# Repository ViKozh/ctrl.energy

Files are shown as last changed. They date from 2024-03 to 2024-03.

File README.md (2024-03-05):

# ctrl.energy
 ESPHome-based node for energy monitoring with additional functionality

## Brief Description
 This module made for my own house as main power meter sensor and gate / outdoor lights control. There're two ESP32 nodes on PCB. One of them performs energy meter monitoring via RS-485 / MODBUS interface. Another one is used to control sliding gates control with Wiegand-based keys and outdoor lights. Also it monitors gate state.

## Hardware
 IMPORTANT!!! Working with HOT LINE AC is dangerous and could harm or even kill! Don't do anything if you don't know how it could behave.
 IMPORTANT 2!!! This hardware works from DC12 power source (J2). It can commutate 5 channels of 16A 230AC via K2-K5 relays.

 You can view PCB and schematic in the _/hardware_ folder in this repository. It was made in KiCAD, so you don't need to buy expensive PCB toolkit to modify or view it. Just keep in mind following mistakes (not the only these, I suppose):
  - Incorrect placements for reed switch based relays (K7 and K8). I've found this error only when recieved produced PCBs - so I decided not to fix it.
  - You'll need better heatsink. LM1084-3.3 could be very hot when powered by 12V. So you should use good thermal interface for it.

 *Note*: PCB successfully soldered and working well (it works almost two weeks.)

## Capabilities

### Energy control node:
  - Temperature monitoring in House Energy Box via D18B20 sensor (J1).
  - Monitor UPS state: battery health (binary sensor) and main power source state (binary sensor) (J3).
  - Monitor state of main power circuit breaker (J4) with auxilary contact like [this](https://automationforum.co/what-is-auxiliary-contact-and-how-it-works-with-mcb/).
  - Monitor case intrusion to House Energy Box via switch connected to J6.
  - Writing logs and settings to microSD card module (J18).
  - Integrated ds3232 RTC clock (EEPROM and alarms functionality is currently not supported by ESPHome) + cr2032 lithium battery.
  - Modbus / RS485 interface via RS485 to UART converter (J12).
  - UART logs from ESP32 (J9).
  - Power Control for Gate control node to reduce power consumption when Main Power source is off the grid.
  - Send messages of problems, daily and monthly report via Telegram Bot (you should create it, see Telegram bot reference to know how to create own telegram bot).

### Gate control node:
  - Control sliding gates in two modes (i.e. full open mode and pedestrian mode) (J16).
  - Sense gate state (opened or closed) with any switch or button (J17).
  - Stores up to 8 Wiegand-26 keys to open gate - use *+ KEY* (SW3) to add a new key, short press *- KEY* (SW4) to remove one key, long press *- KEY* to remove all keys from memory of ESP32.
  - RFID (Wiegand-26 protocol) with J15 pins 5-8.
  - Indicates success or failure with red/green LEDs (J15, pins 2 and 3 as control _ground pins_, pin 1 as +12V power pin for LEDs)
  - Controls up to 5 lamps/zones (*HOT ZONE!!! Up to AC 230v*) - connect AC power source to J5, connect lamps to J7, J8, J10, J11 and J13.

## Configuration

### Energy control node:

  You should configure _secrets.yaml_ to use telegram bot. Both *tg_token_id* and *tg_chat_id* are required for messaging. 

  Set *pincode* to define code to arm/disarm case intrusion protection.

  Set *energy_provider_name* to you Energy Company name or anything else.

  Set *ha_url* to your Home Assistant instance URL and *grafana_url* to Grafana Dashboard. This links will be available in telegram messages.

  Another options are pretty common for ESPHome configs. See _config.yaml_ for all required variables.

### Gate control node:

  This node configuration is also contains common for ESPHome secret variables.

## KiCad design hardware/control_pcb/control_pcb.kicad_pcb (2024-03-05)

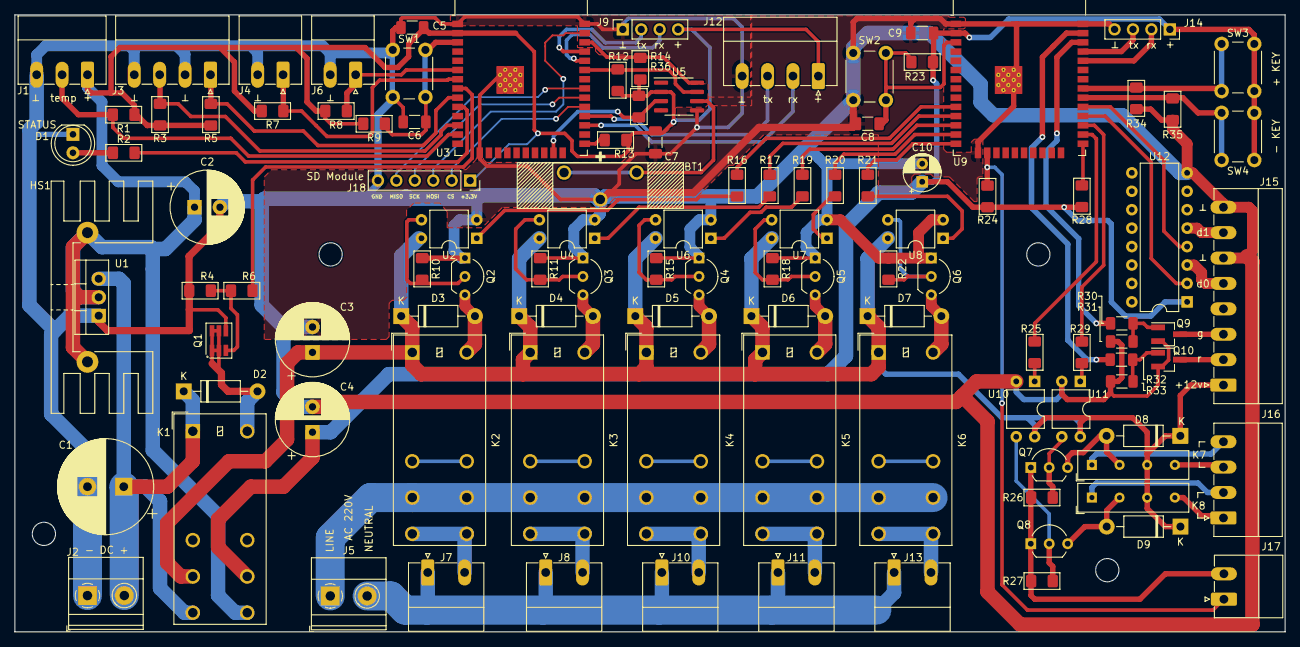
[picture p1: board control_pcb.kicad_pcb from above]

Board: 2 copper layers, 175.0 x 85.0 mm, 109 parts (0 on the bottom side), 85 nets.

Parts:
BT1: CR2032; Battery_Holder_CR2032_Vertical
C1: 1000uF / 50v; CP_Radial_D13.0mm_P5.00mm
C2, C4: 100uF / 16v; CP_Radial_D10.0mm_P3.50mm
C3: 100uF / 50v; CP_Radial_D10.0mm_P3.50mm
C5, C7, C9: 100nF; C_1206_3216Metric_Pad1.33x1.80mm_HandSolder
C6, C8: 1uF; C_1206_3216Metric_Pad1.33x1.80mm_HandSolder
C10: 10uF / 16v; CP_Radial_D5.0mm_P2.50mm
D1: STATUS; LED_D5.0mm_Clear
D2: 1N4002; D_DO-41_SOD81_P10.16mm_Horizontal
D3, D4, D5, D6, D7, D8, D9: 1N4007; D_DO-41_SOD81_P10.16mm_Horizontal
HS1: Heatsink_Pad; Heatsink_Stonecold_HS-132_32x14mm_2xFixation1.5mm
J1: DS18B20 TEMP; PhoenixContact_MC_1,5_3-G-3.5_1x03_P3.50mm_Horizontal
J2: DC12v; TerminalBlock_Phoenix_MKDS-1,5-2-5.08_1x02_P5.08mm_Horizont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
J3: UPS_DETECTION; PhoenixContact_MC_1,5_4-G-3.5_1x04_P3.50mm_Horizontal
J4: INPUT_FUSE_SENSE; PhoenixContact_MC_1,5_2-G-3.5_1x02_P3.50mm_Horizontal
J5: AC IN; TerminalBlock_Phoenix_MKDS-1,5-2-5.08_1x02_P5.08mm_Horizont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
J6: CASE_SENSOR; PhoenixContact_MC_1,5_2-G-3.5_1x02_P3.50mm_Horizontal
J7: Parking; PhoenixContact_MC_1,5_2-G-5.08_1x02_P5.08mm_Horizontal
J8: Front Yard; PhoenixContact_MC_1,5_2-G-5.08_1x02_P5.08mm_Horizontal
J9: EC_RS232; PinSocket_1x04_P2.54mm_Vertical
J10: Bollards; PhoenixContact_MC_1,5_2-G-5.08_1x02_P5.08mm_Horizontal
J11: Address; PhoenixContact_MC_1,5_2-G-5.08_1x02_P5.08mm_Horizontal
J12: MODBUS_UART; PhoenixContact_MC_1,5_4-G-3.5_1x04_P3.50mm_Horizontal
J13: Fence Lights; PhoenixContact_MC_1,5_2-G-5.08_1x02_P5.08mm_Horizontal
J14: LC_RS232; PinSocket_1x04_P2.54mm_Vertical
J15: RFID_READER; PhoenixContact_MC_1,5_8-G-3.5_1x08_P3.50mm_Horizontal
J16: GATES_CONTROL; PhoenixContact_MC_1,5_4-G-3.5_1x04_P3.50mm_Horizontal
J17: GATES_STATE_SWITCH; PhoenixContact_MC_1,5_2-G-3.5_1x02_P3.50mm_Horizontal
J18: SD Module; PinSocket_1x06_P2.54mm_Vertical
K1: G2RL-2; Relay_DPDT_Omron_G2RL-2
K2, K3, K4, K5, K6: G2RL-1-E; Relay_SPDT_Omron_G2RL-1-E
K7, K8: EDR101A1200; Relay_SPST_StandexMeder_MS_Form1AB
Q1: AO6400; SOT-23-6_Handsoldering
Q2, Q3, Q4, Q5, Q6, Q7, Q8: 2N2222; TO-92_Inline_Wide
Q9, Q10: IRLML2402; SOT-23_Handsoldering
R1: 4k7; R_1206_3216Metric_Pad1.42x1.75mm_HandSolder
R2: 68; R_1206_3216Metric_Pad1.42x1.75mm_HandSolder
R3, R4, R5, R7, R8, R9, R10, R11, R12, R13, R14, R15, R18, R22, R23, R24, R26, R27, R28, R34, R35, R36: 10k; R_1206_3216Metric_Pad1.42x1.75mm_HandSolder
R6: 150; R_1206_3216Metric_Pad1.42x1.75mm_HandSolder
R16, R17, R19, R20, R21, R25, R29: 120; R_1206_3216Metric_Pad1.42x1.75mm_HandSolder
R30, R32: 1k; R_1206_3216Metric_Pad1.30x1.75mm_HandSolder
R31, R33: 100k; R_1206_3216Metric_Pad1.30x1.75mm_HandSolder
SW1: EC_RESET; SW_PUSH_6mm
SW2: GLC_RESET; SW_PUSH_6mm
SW3: Write Token; SW_PUSH_6mm
SW4: Delete Token; SW_PUSH_6mm
U1: LM1084-3.3; TO-220-3_Vertical
U2, U4, U6, U7, U8, U10, U11: PC817; DIP-4_W7.62mm
U3, U9: ESP32-WROOM-32; ESP32-WROOM-32D
U5: DS3232M; SOIC-8_3.9x4.9mm_P1.27mm
U12: DIP-16_W7.62mm

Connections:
/+3.3V: C4.1, C9.2, C10.1, J14.1, K1.21, R23.2, R24.1, R28.1, SW3.2, SW4.2, U9.2 (VDD), U12.1 (Vdd)
/+3.3V_PROTECTED: C2.1, C5.2, C7.2, HS1.1, J1.1, J9.4, J12.1, J18.1, K1.24, R1.1, R3.2, R5.2, R7.2, R8.2, R9.2, R12.2, R13.1, R14.2, R36.1, U1.2 (VO), U3.2 (VDD), U5.2 (VCC)
/+12V: C3.1, D3.1 (K), D4.1 (K), D5.1 (K), D6.1 (K), D7.1 (K), D8.1 (K), D9.1 (K), J15.1, K1.11, K2.A1, K3.A1, K4.A1, K5.A1, K6.A1, K7.5, K8.5, U2.4, U4.4, U6.4, U7.4, U8.4, U10.4, U11.4
/Energy Control/AC_LOW: J3.3, R3.1, U3.12 (IO27)
/Energy Control/BAT_LOW: J3.1, R5.1, U3.9 (IO33)
/Energy Control/CASE_OPEN: J6.1, R8.1, U3.6 (IO34)
/Energy Control/EC_M_RX: J12.2, U3.27 (IO16)
/Energy Control/EC_M_TX: J12.3, U3.28 (IO17)
/Energy Control/EC_RX: J9.3, U3.34 (RXD0/IO3)
/Energy Control/EC_TX: J9.2, U3.35 (TXD0/IO1)
/Energy Control/INPUT_FUSE: J4.1, R7.1, U3.7 (IO35)
/Energy Control/INT_TEMP: J1.2, R1.2, U3.13 (IO14)
/Energy Control/SCL: R14.1, U3.36 (IO22), U5.8 (SCL)
/Energy Control/SDA: R12.1, U3.33 (IO21), U5.7 (SDA)
/Energy Control/SD_CS: J18.2, U3.29 (IO5)
/Energy Control/SD_MISO: J18.5, U3.31 (IO19)
/Energy Control/SD_MOSI: J18.3, U3.37 (IO23)
/Energy Control/SD_SCK: J18.4, U3.30 (IO18)
/Energy Control/TACT_FREQ: R36.2, U3.23 (IO15), U5.3 (~INT/SQW)
/LIGHT_00: R16.1, U9.10 (IO25)
/LIGHT_01: R17.1, U9.11 (IO26)
/LIGHT_02: R19.1, U9.12 (IO27)
/LIGHT_03: R20.1, U9.13 (IO14)
/LIGHT_04: R21.1, U9.14 (IO12)
/Lights Relays/LINE: J5.1, K2.11, K3.11, K4.11, K5.11, K6.11
/Lights Relays/NEUTRAL: J5.2, J7.1, J8.1, J10.1, J11.1, J13.1
/OPEN_GATE: R25.2, U9.26 (IO4)
/OPEN_PEDS: R29.2, U9.27 (IO16)
/POW_CTRL: R6.1, U3.8 (IO32)
/SENS_GATE: J17.1, R24.2, U9.16 (IO13)
/WD_0: U9.28 (IO17), U12.2 (Out_A)
/WD_1: U9.29 (IO5), U12.4 (Out_B)
/WLED_GREEN: R30.1, U9.36 (IO22)
/WLED_RED: R32.1, U9.37 (IO23)
/Wiegand Converter/LED_CTRL_GREEN: J15.3, Q9.3 (D)
/Wiegand Converter/LED_CTRL_RED: J15.2, Q10.3 (D)
/Wiegand Converter/WIEGAND_D0: J15.5, U12.3 (In_A)
/Wiegand Converter/WIEGAND_D1: J15.7, U12.5 (In_B)
GND: BT1.2 (-), C1.2, C2.2, C3.2, C4.2, C5.1, C6.2, C7.1, C8.2, C9.1, C10.2, D1.1 (K), J1.3, J2.1, J3.2, J3.4, J4.2, J6.2, J9.1, J12.4, J14.4, J15.6, J15.8, J17.2, J18.6, Q1.4 (S), Q2.1 (E), Q3.1 (E), Q4.1 (E), Q5.1 (E), Q6.1 (E), Q7.1 (E), Q8.1 (E), Q9.2 (S), Q10.2 (S), R4.2, R10.1, R11.1, R15.1, R18.1, R22.1, R26.2, R27.2, R31.1, R33.1, R34.1, R35.1, SW1.1, SW2.1, U1.1 (GND), U2.2, U3.1 (GND), U3.15 (GND), U3.38 (GND), U3.39 (GND), U4.2, U5.5 (GND), U6.2, U7.2, U8.2, U9.1 (GND), U9.15 (GND), U9.38 (GND), U9.39 (GND), U10.2, U11.2, U12.8 (Vss)
unnamed: BT1.1 (+), U5.6 (VBAT)
unnamed: D1.2 (A), R2.1
unnamed: D2.2 (A), K1.A2, Q1.1 (D), Q1.2 (D), Q1.5 (D), Q1.6 (D)
unnamed: C1.1, D2.1 (K), J2.2, K1.14, K1.A1, U1.3 (VI)
unnamed: D3.2 (A), K2.A2, Q2.3 (C)
unnamed: D4.2 (A), K3.A2, Q3.3 (C)
unnamed: D5.2 (A), K4.A2, Q4.3 (C)
unnamed: D6.2 (A), K5.A2, Q5.3 (C)
unnamed: D7.2 (A), K6.A2, Q6.3 (C)
unnamed: D8.2 (A), K7.3, Q7.3 (C)
unnamed: D9.2 (A), K8.3, Q8.3 (C)
unnamed: J7.2, K2.14
unnamed: J8.2, K3.14
unnamed: J10.2, K4.14
unnamed: J11.2, K5.14
unnamed: J13.2, K6.14
unnamed: J14.2, U9.34 (RXD0/IO3)
unnamed: J14.3, U9.35 (TXD0/IO1)
unnamed: J16.1, K8.7
unnamed: J16.2, K8.1
unnamed: J16.3, K7.7
unnamed: J16.4, K7.1
unnamed: Q1.3 (G), R4.1, R6.2
unnamed: Q2.2 (B), R10.2, U2.3
unnamed: Q3.2 (B), R11.2, U4.3
unnamed: Q4.2 (B), R15.2, U6.3
unnamed: Q5.2 (B), R18.2, U7.3
unnamed: Q6.2 (B), R22.2, U8.3
unnamed: Q7.2 (B), R26.1, U11.3
unnamed: Q8.2 (B), R27.1, U10.3
unnamed: Q9.1 (G), R30.2, R31.2
unnamed: Q10.1 (G), R32.2, R33.2
unnamed: R16.2, U2.1
unnamed: R17.2, U4.1
unnamed: R19.2, U6.1
unnamed: R20.2, U7.1
unnamed: R21.2, U8.1
unnamed: R25.1, U10.1
unnamed: R29.1, U11.1
unnamed: C6.1, R9.1, SW1.2, U3.3 (EN)
unnamed: R13.2, U3.25 (IO0)
unnamed: R2.2, U3.10 (IO25)
unnamed: C8.1, R23.1, SW2.2, U9.3 (EN)
unnamed: R28.2, U9.25 (IO0)
unnamed: R35.2, SW4.1, U9.30 (IO18)
unnamed: R34.2, SW3.1, U9.31 (IO19)

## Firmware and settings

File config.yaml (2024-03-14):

substitutions:
  voltage_normal: '230'
  supported_load_level: '32'
  voltage_min_bound: '120'
  voltage_max_bound: '280'
  voltage_warning_lower_level: '170'
  voltage_warning_upper_level: '240'
  voltage_failure_lower_level: '150'
  voltage_failure_upper_level: '270'
  phase_shift_warning_level: '5.0'
  phase_shift_failure_level: '20.0'
  overload_warning_level: '5.0'
  overload_failure_level: '20.0'
  energy_source_name: !secret energy_provider
  tg_bot_token: !secret tg_token_id
  tg_chat_id: !secret tg_chat_id
  grafana_url: !secret grafana_url
  ha_url: !secret ha_url
  case_pincode: !secret pincode

esphome:
  name: energy-control
  comment: Energy Control
  project:
    name: "vks.control_energy"
    version: "1.1"
  libraries:
    - SPI
    - FS
    - SD
    - FFat
    - ArduinoJson
  includes:
    - csv_strings.h
    - tg_bot_strings.h
    - log_strings.h
    - sdcard.h
    - settings.h
    - problems.h
    - snapshot.h
  platformio_options:
    build_flags: -DFS_NO_GLOBALS
    lib_ldf_mode: deep+    
  on_boot:
    priority: 600
    then:
      - ds1307.read_time: rtc_clock
      - if:
          condition:
            - lambda: return id(disable_deep_sleep);
          then:
            - deep_sleep.prevent: dsleep
      - lambda: |-
          setupProblems();

          //Set Generic Power Failure to warning (undefined state) until connection to MODBUS sensor is stabilized or failed.
          setProblem(Problems::GENERIC_POWER_FAILURE, ProblemState::WARNING);
          ESP_LOGI("Energy Meter", "Is module offline? %s", YESNO(id(main_energy_meter).get_module_offline()));

          id(card_available) = SD.begin(5);

          if(!id(card_available)) {
            ESP_LOGW("SD", "Unable to mount SD card.");
          } else {
            sdcard::writeLogfile(id(rtc_clock).utcnow(), LOG_EVENT_TYPE_INFO, LOG_CATEGORY_NODE, "Node is starting...");
          }

          settings::storage = &id(system_settings)[0];
          ESP_LOGD("Settings", "Loading settings...");
          if(!settings::readSettings()) {
            ESP_LOGE("Settings", "Unable to initialize settings data.");
          }
          

          auto counter = id(em_x_total_counter).state;
          for(int i = 0; i < sizeof(snapData.data); i++) {
            snapData.data[i] = id(snapshot_data)[i];
          };
          if(!isfinite(counter)) {
            ESP_LOGW("Counter", "Power meter consumption counter data is unavailable. Maybe counter is offline?");
          }
          loadFromSnapshot(counter);

          
          add_on_failure_callback([](Problems problem) { 
            id(process_problem).execute(
              static_cast<int>(problem),
              static_cast<int>(ProblemState::FAILURE)
              ); });
          add_on_warning_callback([](Problems problem) { 
            id(process_problem).execute(
              static_cast<int>(problem), 
              static_cast<int>(ProblemState::WARNING)
              ); });
          add_on_restore_callback([](Problems problem) { 
            id(process_problem).execute(
              static_cast<int>(problem),
              static_cast<int>(ProblemState::NONE)
              ); });

          if(!id(card_available)) {
            ESP_LOGW("SD", "Unable to mount SD card.");
          } else {
            sdcard::writeLogfile(id(rtc_clock).utcnow(), LOG_EVENT_TYPE_INFO, LOG_CATEGORY_NODE, "Node has been started.");
          }
      - delay: 2s
      - wait_until:
          condition:
            lambda: return id(rtc_clock).now().is_valid();
      - lambda: |-
          id(is_loaded) = true;
          startMonitoring();
  on_shutdown:
    priority: 400
    then:
      - lambda: |-
          if(!id(is_loaded)) {
            ESP_LOGE("Node", "Invalid system state. Shutdown is initialized before node has been loaded.");
            return;
          };

          stopMonitoring();

          if(!id(card_available)) {
            ESP_LOGW("SD", "Unable to mount SD card.");
            return;
          } else {
            sdcard::writeLogfile(id(rtc_clock).utcnow(), LOG_EVENT_TYPE_INFO, LOG_CATEGORY_NODE, "Node will be shutted down (deep sleep or connectivity loss).");
            saveToSnapshot(id(em_x_total_counter).state);
            for(int i = 0; i < sizeof(snapData.data); i++) {
              id(snapshot_data)[i] = snapData.data[i];
            };
            ESP_LOGD("Settings", "Saving settings to SD Card...");
            if(!settings::writeSettings()) {
              ESP_LOGE("Settings", "Unable to save settings data.");
            }
          };
          sdcard::writeLogfile(id(rtc_clock).utcnow(), LOG_EVENT_TYPE_INFO, LOG_CATEGORY_NODE, "Gracefully shut down.");


esp32:
  board: esp32dev
  framework:
    type: arduino
    version: 2.0.14
    platform_version: 6.5.0

logger:
  level: INFO

dallas:
  - pin: GPIO14
    id: case_temp
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

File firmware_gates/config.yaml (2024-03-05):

esphome:
  name: gateway-control
  comment: Gateway Control
  project:
    name: "vks.control_gateway"
    version: "1.0"

esp32:
  board: esp32dev

logger:

globals:
  - id: max_keys
    type: int
    restore_value: false
    initial_value: '8'
  - id: stored_keys
    type: int[8]
    restore_value: true
    initial_value: '{-1,-1,-1,-1,-1,-1,-1,-1}'
  - id: last_access_time
    type: int[8]
    restore_value: true
    initial_value: '{-1,-1,-1,-1,-1,-1,-1,-1}'
  - id: last_access_date
    type: int[8]
    restore_value: true
    initial_value: '{-1,-1,-1,-1,-1,-1,-1,-1}'
  - id: key_read
    type: bool
    restore_value: false
    initial_value: 'false'
  - id: service_mode
    type: bool
    restore_value: false
    initial_value: 'false'
  - id: current_key
    type: uint64_t
    restore_value: false
    initial_value: '-1'
  - id: last_used_card
    type: int
    restore_value: true
    initial_value: '-1'
  - id: last_access
    type: std::string
    restore_value: true
    initial_value: '""'
    max_restore_data_length: 32


api:
  encryption:
    key: !secret enc_key
  reboot_timeout: 30s

mqtt:
  id: mqtt_service
  broker: !secret mqtt_broker
  port: 1883
  username: !secret mqtt_usr
  password: !secret mqtt_pwd
  discovery: false
  topic_prefix: !secret mqtt_prefix
  keepalive: 5s

ota:
  password: !secret ota_password

wifi:
  networks:
    - ssid: !secret wifi_name
      password: !secret wifi_pwd
    - ssid: !secret wifi_name_bak
      password: !secret wifi_pwd_bak
  power_save_mode: none
  ap:
    ssid: "VKS_GC"
    password: !secret wifi_pwd_ap

captive_portal:

time:
  - platform: sntp
    id: ntp_time

output:
  - platform: gpio
    id: gate_full
    pin: GPIO4
  - platform: gpio
    id: gate_ped
    pin: GPIO16
  - platform: gpio
    id: lt_parking
    pin: GPIO25
  - platform: gpio
    id: lt_front_yard
    pin: GPIO26
  - platform: gpio
    id: lt_bollards
    pin: GPIO27
  - platform: gpio
    id: lt_address
    pin: GPIO14
  - platform: gpio
    id: lt_fence
    pin: GPIO12
  - platform: gpio
    id: led_rfid_green
    pin: 
      number: GPIO22
      mode: 
        pulldown: true
        output: true
  - platform: gpio
    id: led_rfid_red
    pin: 
      number: GPIO23
      mode: 
        pulldown: true
        output: true

binary_sensor:
  - platform: gpio
    id: card_add
    pin: GPIO19
    name: "Add Card"
    device_class: ""
    internal: true
    on_click:
      min_length: 1s
      max_length: 5s
      then:
        - script.execute:
            id: key_add
  - platform: gpio
    id: card_remove
    pin: GPIO18
    name: "Remove [All] Card[-s]"
    internal: true
    device_class: ""
    on_click:
      - min_length: 1s
        max_length: 5s
        then:
          - script.execute:
              id: key_remove
      - min_length: 5s
        max_length: 10s
        then:
          - script.execute:
              id: key_clear    
  - platform: gpio
    pin: GPIO13
    name: "Main Gate"
    device_class: door
    icon: mdi:gate

wiegand:
  - id: rfid_panel
    d0: GPIO17
    d1: GPIO5
    on_raw:
      then:
        - lambda: |-
            auto check_eparity = [] (uint64_t value, int start, int length) {
              int parity = 0;
              uint64_t mask = 1LL << start;
              for (int i = 0; i < length; i++, mask <<= 1) {
                if (value & mask)
                  parity++;
              }
              return !(parity & 1);
            };

            auto check_oparity = [] (uint64_t value, int start, int length) {
              int parity = 0;
              uint64_t mask = 1LL << start;
              for (int i = 0; i < length; i++, mask <<= 1) {
                if (value & mask)
                  parity++;
              }
              return parity & 1;
            };

            if(id(key_read))
            {
              ESP_LOGW("KEYS", "Key has been already read. Please wait for clean up.");
              return;
            }

            if(bits != 26)
            {
              ESP_LOGW("KEYS", "Unsupported key (%d bits) has been read: %llx", bits, value);
              id(key_read) = false;
              id(current_key) = -1;
              return;
            };

            if (!check_eparity(value, 13, 13) || !check_oparity(value, 0, 13)) {
              ESP_LOGW("KEYS", "Invalid parity for key: %llx", value);
              id(key_read) = false;
              id(current_key) = -1;
              return;
            }

            id(current_key) = (value >> 1) & 0xffffff;

            ESP_LOGI("RFID", "Tag has been read: %llx", id(current_key));

            id(key_read) = true;
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

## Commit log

2024-03-05 Ready for testing
    Implemented core functionality for ESP32-based node
2024-03-05 Added supplemental projects and updated README
    [control_pcb.kicad_pcb, control_pcb.kicad_sch, e_control.kicad_sch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]
2024-03-11 Various fixes after testing
    I've made a lot of fixes after testing on the working prototype of hardware.
    [config.yaml, csv_strings.h, problems.h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]
2024-03-12 Settings has been moved to internal memory
    Fixed logic for select component though it seems to work unexpectable.
    [config.yaml, settings.h]
2024-03-13 Fix to min/max monitoring and total power failure duration.
    [config.yaml, problems.h, settings.h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]
2024-03-14 Fixed logic for problems handling
    [config.yaml, problems.h, snapshot.h]
